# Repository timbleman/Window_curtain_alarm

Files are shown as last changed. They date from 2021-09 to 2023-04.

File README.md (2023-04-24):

# Window curtain alarm

## Basics
This project aims at creating an alarm that opens and closes a window curtain at certain times each weekday. The system is connected to the local network and is configured using socket communication. The alarm operates independently, it does not require a hub or external control, wake and sleep times can be set for each weekday. An internet connection is required.
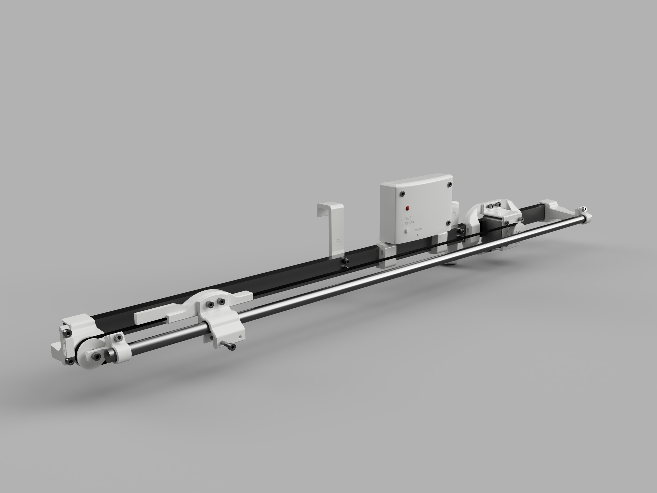
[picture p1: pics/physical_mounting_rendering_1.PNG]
Rendering of the physical hardware Hardware rendering.

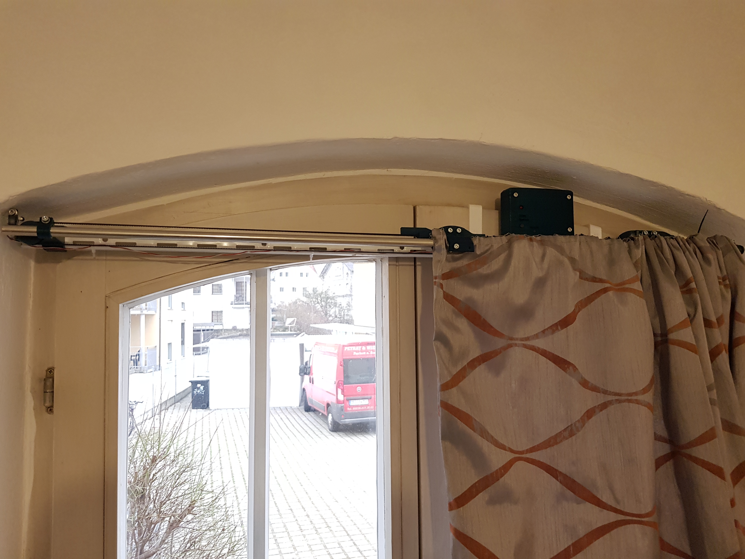
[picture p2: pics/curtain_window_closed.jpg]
Installed hardware. Window can still be opened.


## Changelog
* V1.2: Added OTA updating, WiFi connection using WPS and Serial, refactorings, a BOM and some UML diagrams.
* V1.1: Added a locally accessible, basic webpage. Improved 3D files slightly. Minor bug fixes.
* V1.0: Initial release. Controls using a hardware button and a TCP socket.

## Features
### Implemented features
* Automatically keeping track of time
* One wake and sleep time for each weekday
* Belt-driven opening and closing of curtains
* WiFi configuration using WPS, Serial interface or source code
* Socket-based user communication
* Local webpage for communication
* Over the air updating
* Button for snoozing one day and manually opening and closing the curtain
* PCB design
* STL files for assembling the project
### Possible future work
* Multiple wake and sleep times for each weekday
* Different endstop locations
* Using more advanced features of the TMC2209 stepper driver (e.g.: sensorless homing)
* Sync multiple curtains 
### Intentional limitations
* Only accessible in the local network
* No secure communication

## Usage
### Setup
Install the system according to the readme in /3D_objects/. In this directory there is also a bill of materials. You can adjust the SSID and password in the code. Compile and upload or just upload the binary.
Connect a 5V 2A power supply. If you have not provided your SSID in the code, you have two options: Firstly, you connect a Serial terminal with 9600 baud rate and enter your data. Secondly, you can use WPS if your router supports it. Press the WPS button of your router, then the button of the window_curtain_alarm, wait approximately 30 seconds and then restart the ESP.  
Assign a static IP using your router. You will need this IP to connect to the system. The IP is also printed using VCP at power-up.
### Basic controls using TCP sockets
This alarm can be configured using the telnet protocol. Connect using the IP and port 23 with a client of your choice.
Sending "help" gets a list of example commands.  
Upon powering up, the curtain position has to be calibrated. Open the curtain to the desired position by hand and 
send "calibrate". Make sure the motor moves in the right direction and hits the endstop. 
Now everything should be ready to go. Use "set_wake" and "set_sleep" to set the alarm. Check if the times have been correctly 
set using "waketimes" and "sleeptimes". Check if the right timezone is selected using "curtime".
You can manually move the curtain using "open", "close" or "curtainxor".  

<p float="left">
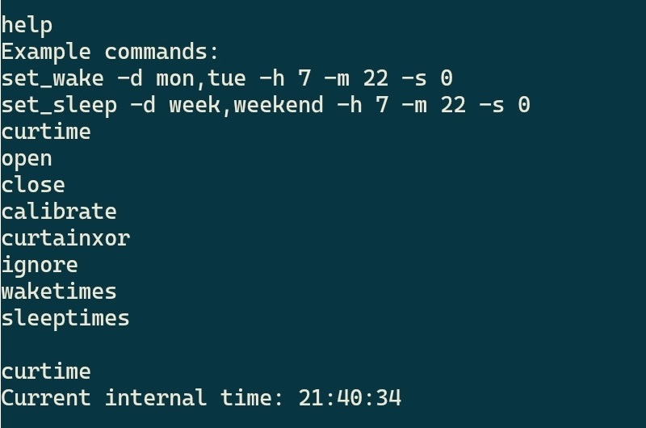
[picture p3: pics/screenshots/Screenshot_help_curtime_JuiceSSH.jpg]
  
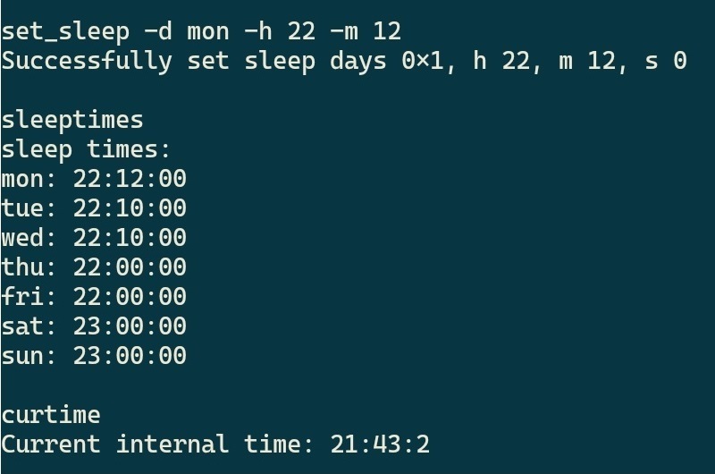
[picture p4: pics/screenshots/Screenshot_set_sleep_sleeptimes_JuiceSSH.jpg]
   
</p>

### Controls using the webpage
With version 1.1, a crude webpage is now available. Please don't judge the interface too harshly. :)  
The webpage is hosted locally and has the same functionality, as the command line style TCP interface. 
D-pad-like buttons allow you to move the curtain, ignore the next wake or calibrate.
Below, the current wake or sleep times are shown and can be changed.
The webpage should work on desktop and mobile. Some of the code has been taken from this [great post](https://gist.github.com/bbx10/667e3d4f5f2c0831d00b).  
You can update code when visiting IP:8000/update!
<p float="left">
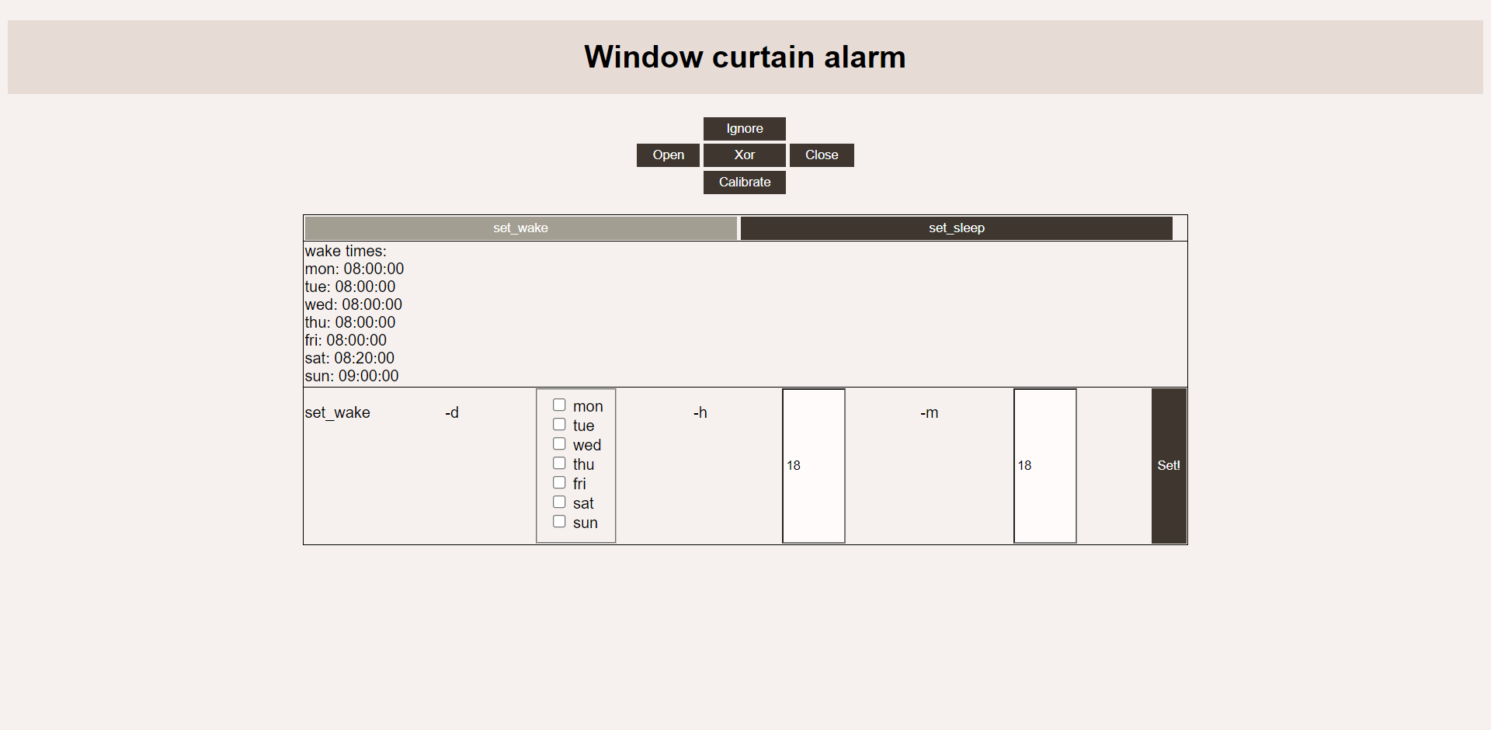
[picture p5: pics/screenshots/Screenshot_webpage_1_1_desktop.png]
  
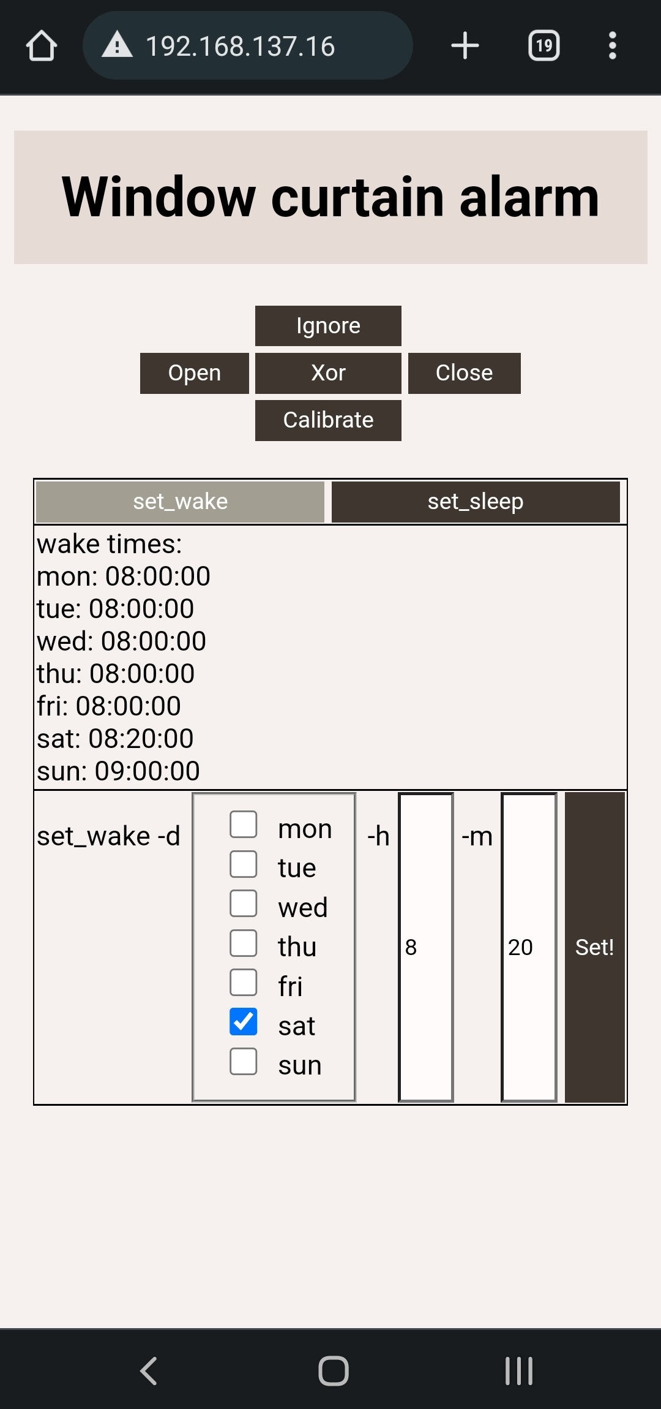
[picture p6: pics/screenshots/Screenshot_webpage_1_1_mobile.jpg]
   
</p>

### Controls using only the hardware
You can XOR the curtainstate by short pressing the hardware button, long pressing ignores the next wake.
An LED indicates if a short or a long press has been detected.

## Project structure
Here are some directories that may contain interesting files:
* /3D_objects/: 3D-printable objects and installation instructions.
* /course_python_draft/: This quick python prototype aims at visualizing the core concepts and ideas of the project. Untested.
* /curtain_wiring/: A KiCad project for the wiring diagram and PCB design.
* /esp8266_code/actual_project/: The unit tested proof of concept code ported to ESP8266.
* /esp8266_code/test_stuff/: Some quick projects testing basic functionality using the ESP8266.
  * /esp8266_code/test_stuff/socket_test/: TCP socket server test project for the ESP8266.
  * /esp8266_code/test_stuff/motor_test/: Homing and moving using the TMC2209 driver.
* /proof_of_concept/: Unit tested project implementing generic components. This project does not strictly target embedded hardware for ease of building and debugging.
* /pics/: Some pictures, diagrams and renderings.

## Implementation
### Hardware
Opening and closing the curtain is done using a belt driven by a stepper motor. A NEMA17 stepper in combination with a TMC2209 driver is currently used. The target platform is the ESP8266. This microcontroller has been chosen instead of a Raspberry PI due to its lower cost and power consumption. 
### Mounting
The hardware, including especially the motor, belt, and endstop, will be mounted using 3D printed objects. Currently, the project is not intended as a 'one design fits all' solution, but will need to be adapted to the used curtain and window.
### Programming language and environment
Due to its dominance in embedded systems and easier debugging, C, instead of C++, is used for most of the more generic project components. These components include user input parsing, keeping track of time, and controlling the IO.
As Arduino and most of its libraries are based on C++, the main function and socket server use this more high-level approach. The PlatformIO IDE and toolchain is used for the ESP8266 code. The unit tested proof of concept has been developed using CodeLite.  

The following class diagram should give an overview of the projects components.  As C, the language most used in this project is not class-oriented, I deviated slightly from the UML standard. Instead of modeling classes, I model files, structs, and enums. Enums are often used by multiple files, this is not modeled to increase readability.
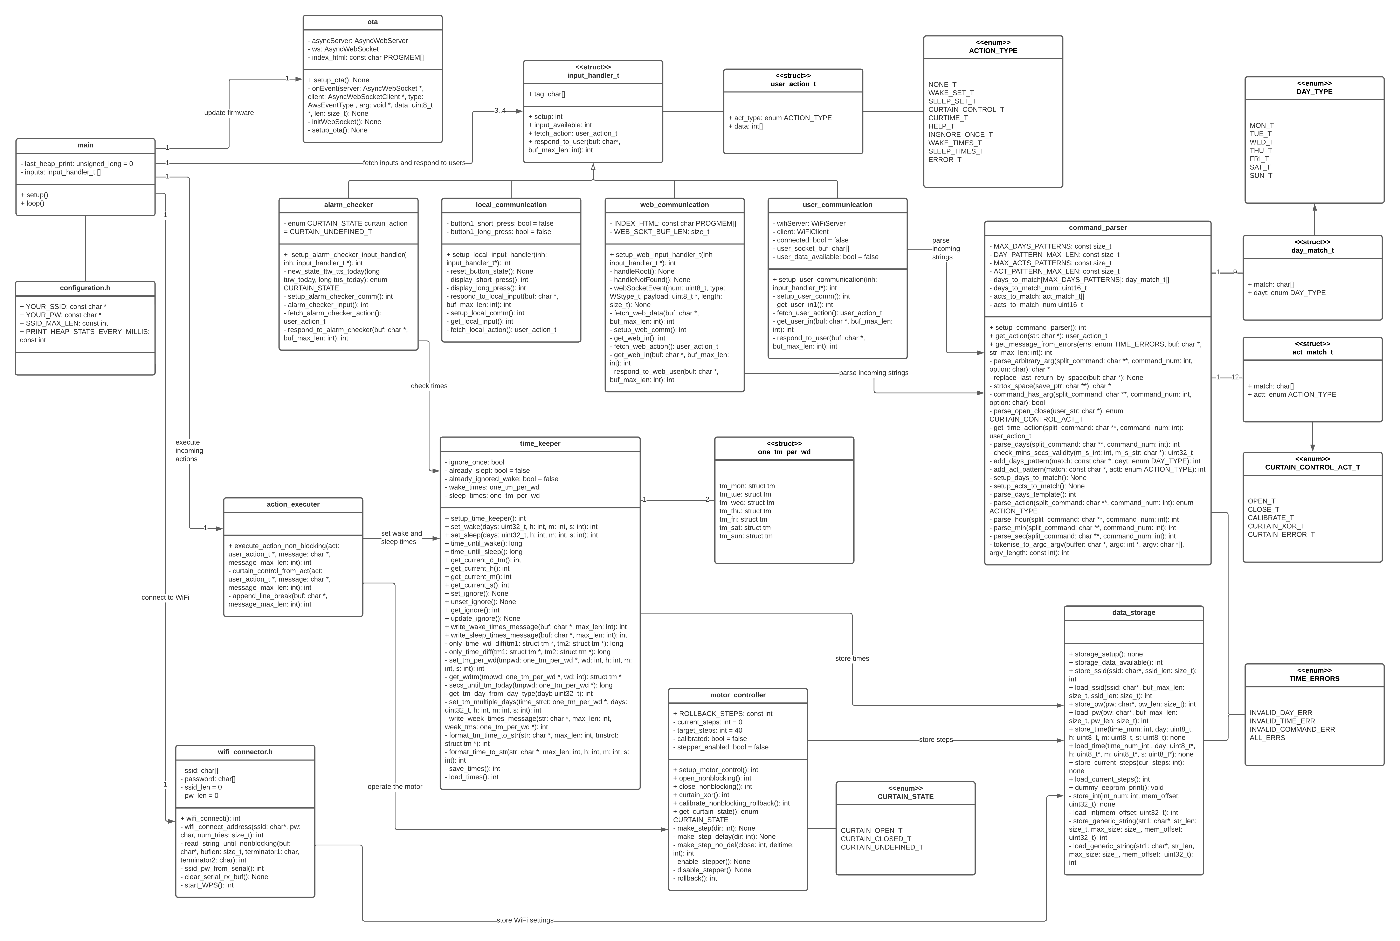
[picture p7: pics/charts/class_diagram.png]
A class diagram.

### Testing
The uCunit framework has been used for unit testing portable code components. The framework is basic but very portable and requires only a few header files.

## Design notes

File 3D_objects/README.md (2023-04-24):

# 3D objects and mounting

This subfolder stores 3D objects used to mount and build the curtain closer alarm.
The objects have been designed using Fusion360 and saved as STLs. Step files are also included.

## Project structure
These directories contain the 3D models:
* /electronics_mount/: Mounts for the board and the motor. Also includes the pulley and belt components.
* /motor_and_belt/: Components to install the Nema 17 and gt2 belt.
* /mount_curved_window/: Mounting brackets for a curved window. Will need to be adapted to your setup.
* /mount_rail/: Basic mounts for the rail. Includes end stop mount.

## Installation
### Needed components
You will need metric m4 screws of the following lengths: 10mm, 16mm, and 30mm. M3x6mm screws are also needed. You will also need square m4 nuts with dimensions of 7x7x2mm. The curtain rail has a diameter of 12mm. The flat u-shaped rail to mount all the components can be found in most German hardware stores. A 6mm wide gt2 belt and 684zz bearings are needed to move the curtain. Please look up the required electronic components in the wiring diagram. Have a look at the bill of meterials below, to find needed components.  

#### BOM
| Part name | Quantity | Price [€] |
|---|---|---|
| **Electronics** | | |
| ESP8266 NodeMCU ESP-12F | 1 | 5 |
| NEMA17 (max depth 34mm) | 1 | 7 |
| TMC2209 V2 | 1 | 3 |
| Board | 1 | 2 |
| R 100 Ohm | 1 | 0.01 |
| R 1 kOhm | 3 | 0.01 |
| R 10 kOhm | 2 | 0.01 |
| C 100 uF | 1 | 0.01 |
| C 220 uF | 1 | 0.01 |
| C 100 nF | 2 | 0.01 |
| LED 5mm | 1 | 0.01 |
| Button 12x12 | 1 | 0.01 |
| Pin headers m/f | Several  | 0.2 |
| Micro USB Cable | 1 | 5 |
| USB wall plug | 1 | 5 |
| **3D Printing** | | |
| Filament (PLA/PETG) | 200g | 4 |
| **Screws** | | |
| M3x6 | 4 | 0.1 |
| M4x4 grub screw | 1 | 0.1 |
| M4x10 | 22 | 0.3 |
| M4x16 | 4 | 0.1 |
| M4x30 | 3 | 0.1 |
| M4 7x7x2 square nuts | 29 | 0.2 |
| M4 washers | 25 | 0.2 |
| **Mounting** | | |
| GT2 belt 6mm | 3m | 3 |
| 684zz bearings | 2 | 2 |
| Curtain rod 12mm | 1.5m | 5 |
| Rail 10001 | 1.5m | 6 |
| **Total** | | ~50€ |

### Printing
As many of the components are under constant (but not very big) load, I would go with PETG instead of PLA, due to possible creep. The optimal print orientation should be obvious for most parts. Supports should only be needed for the belt connector. An end cap can be printed using TPU to prevent the metal curtain rail from directly hitting the wall. The beam holders require the m4 nuts to be inserted while printing. Remember to add pauses in the slicer! About 200g of Filament are needed.

### Installing everything
Cut the rails to the appropriate length and mount printed components using the m4 screws and nuts. Insert the curtain.
Mount the motor, the pulley, the roller with inserted bearings, and the gt2 belt. Tighten the belt either using the belt connector or the sliding motor mount. Solder components to the board. Install all electronic components. Mount the rail to your desired location and connect a micro USB cord to the NodeMCU.

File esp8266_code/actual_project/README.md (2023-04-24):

# Curtain closer alarm ESP8266 code
This directory contains the proof_of_concept curtain closer code adapted to the ESP8266, specifically the NodeMCU V3.

## Files of interest:
To get a quick overview, I will list which files do what. To keep it compact, only the headers are listed:
* /src/hardware_specific_code/: Code specifically written for the ESP.
    * /src/hardware_specific_code/networking/:
        * /src/hardware_specific_code/web_server/: Local website, webserver and websocket for user communication. Needs arduinoWebSockets library. OTA updating code.
        * user_communication.h: Handles TCP socket setup and communication.
        * wifi_conector.h: onnect to WiFi using SSID stored in EEPROM, specified at compiletime, Serial or WPS. 
    * /src/hardware_specific_code/local_hardware/:
        * data_storage.h: Stores the configuration. Uses the EEPROM library.
        * local_communication.h: Local (hardware, button) input and display.
        * motor_controller.h: This file handles the calibration and operation of the motor.
* /src/portable_code/: Portable, unit tested code.
    * action_executer.h: Executes an action created by the command_parser.
    * alarm_checker.h: Checks whether the curtain should be opened or closed now. Has to be called in a loop. 
    * command_parser.h: Here user input strings are parsed into an action type.
    * time_keeper.h: Saves wake and sleep times for each weekday. Keeps track of time.
    * types_and_enums.h: Type and enum definitions that are shared between multiple components.
* /src/configuration.h: Configures project build and testsuite execution.
* /src/main.cpp: This is the main file running the main loop.

## Configuration
There are some configuration parameters.
SSID and your WIFI password can be set in *configuration.h*. You can also skip this step and directly throw the binary on the ESP and connect to WiFi via Serial or WPS. Look at the main README.md for further instructions.  
The UTC time offset will need to be set in main.c using the `setenv()` function.  
The speed of the stepper motor can be adjusted in motor_controller.c using `FAST_STEP_TIME` and `SLOW_STEP_TIME`.  
Most prints can be disabled using define statements.

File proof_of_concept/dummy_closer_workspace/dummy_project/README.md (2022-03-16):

# Window curtain alarm proof of concept

## Intro
This project serves as a quick prototype for a window curtain alarm.
Basic functions are implemented and tested without the actual hardware:
Parsing strings, setting, and keeping track of time will be fully implemented.
New code should be tested at first in this project before being ported to a MCU.
The motor control and socket interaction will only be implemented as a dummy, as these are highly platform-dependent.
Extensive unit testing using the uCUnit framework should reduce the amount of debugging on the embedded platform.

## Files and contents
This section quickly discusses the files and their contents.
For simplicity reasons, only the h-file is described, not the implementation.
* action_executer.h: Executes an action created by the command_parser.
* alarm_checker.h: Checks whether the curtain should be opened or closed now. Has to be called in a loop. 
* command_parser.h: Here user input strings are parsed into an action type.
* configuration.h: Configures project build and test suite execution.
* data_storage.h: A dummy file to test storing data. Resembles the EEPROM library. 
* main.c: This is the main file running the main loop.
* motor_controller.h: This file handles the calibration and operation of the motor.
* System.c: This file is for the uCUnit framework. The print function has to be changed when porting. 
* Testsuite.h: The actual test cases run by the uCUnit framework. 
* time_keeper.h: Saves wake and sleep times for each weekday. Keeps track of time.
* types_and_enums: Type and enum definitions that are shared between multiple components.
* uCUnit-v1.0.h: A lightweight unit testing framework.

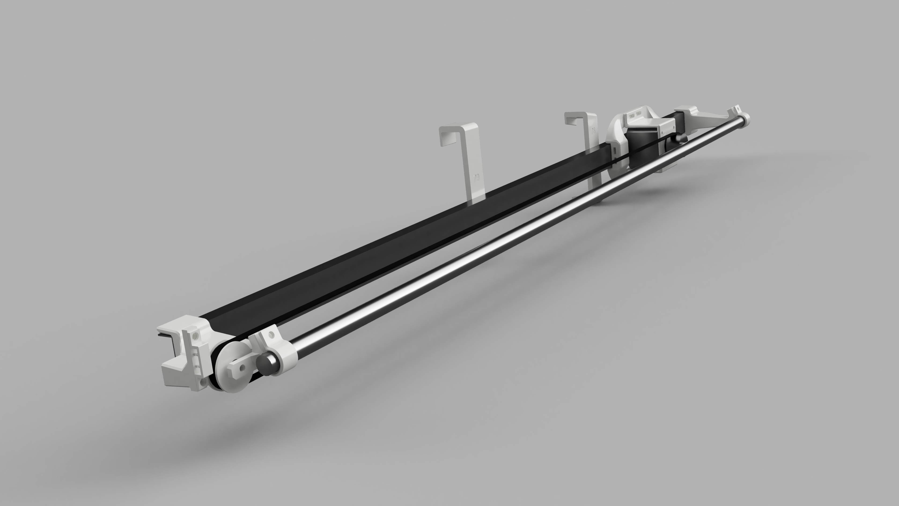
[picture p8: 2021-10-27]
pics/physical_mounting_rendering.PNG

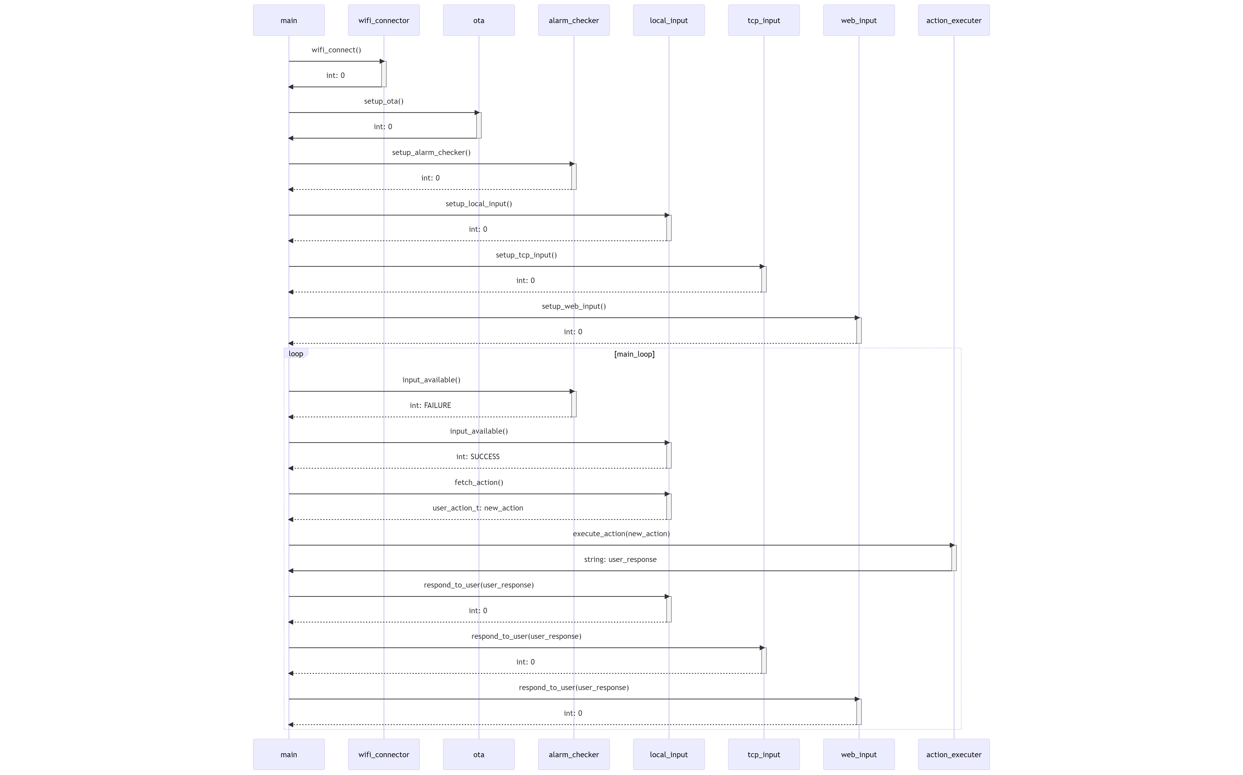
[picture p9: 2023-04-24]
pics/charts/main_flow_chart.png

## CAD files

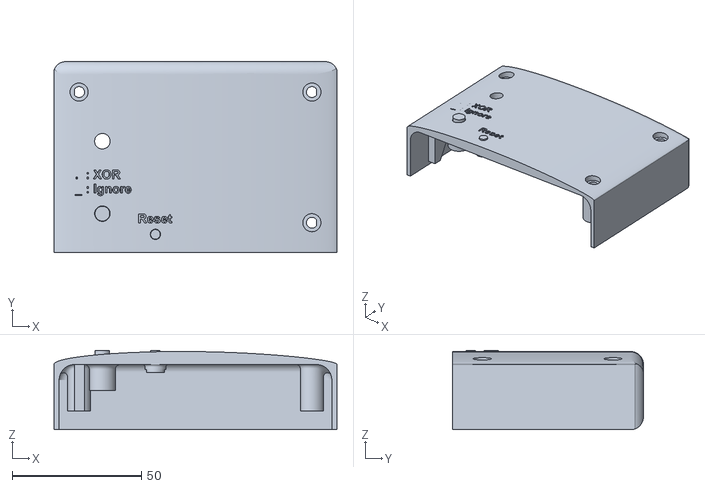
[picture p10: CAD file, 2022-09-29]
3D_objects/electronics_mount/pcb_cover_v1_1.stl
109.4 x 73.8 x 30.7

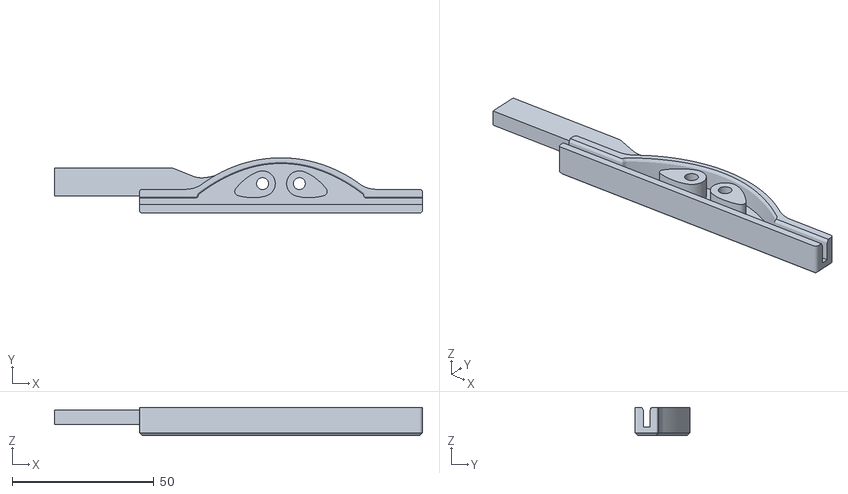
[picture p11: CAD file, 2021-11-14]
3D_objects/motor_and_belt/belt_connector_v1.stl
130.0 x 19.5 x 10.00

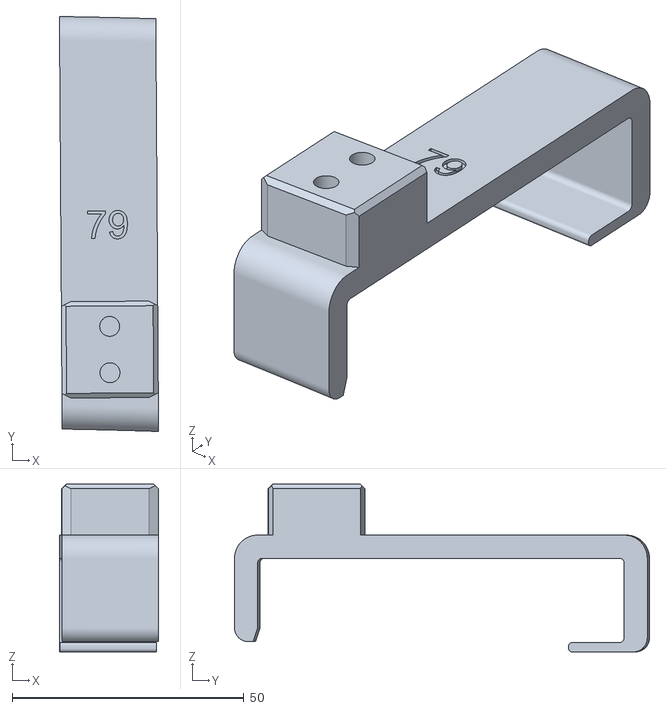
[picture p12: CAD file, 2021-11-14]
3D_objects/mount_curved_window/leftmost_holder_78_v1.stl
21.4 x 89.5 x 36.2

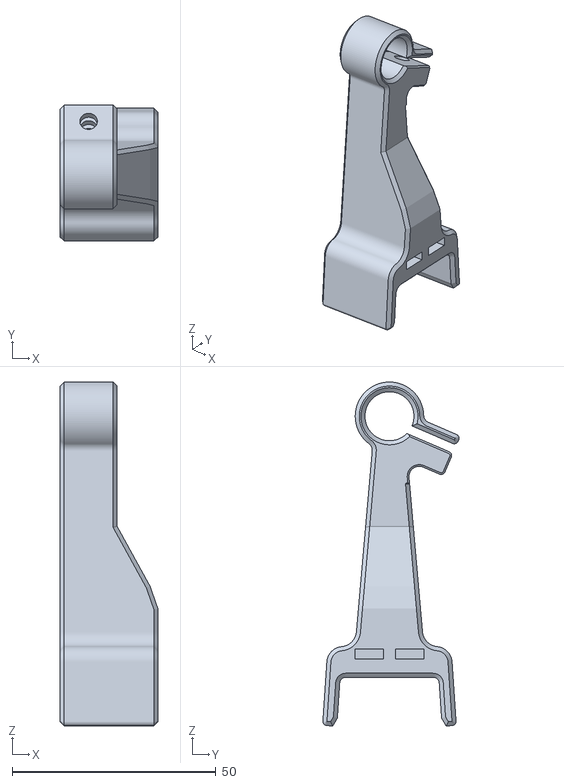
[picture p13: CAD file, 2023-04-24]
3D_objects/mount_rail/beam_holder_r_longer_v1_2.stl
24.0 x 33.4 x 84.3

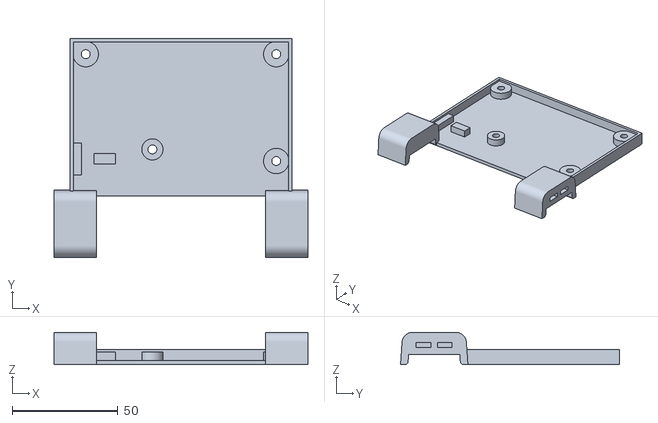
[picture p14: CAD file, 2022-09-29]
3D_objects/electronics_mount/pcb_holder_v1_1.stl
120.0 x 103.5 x 15.3

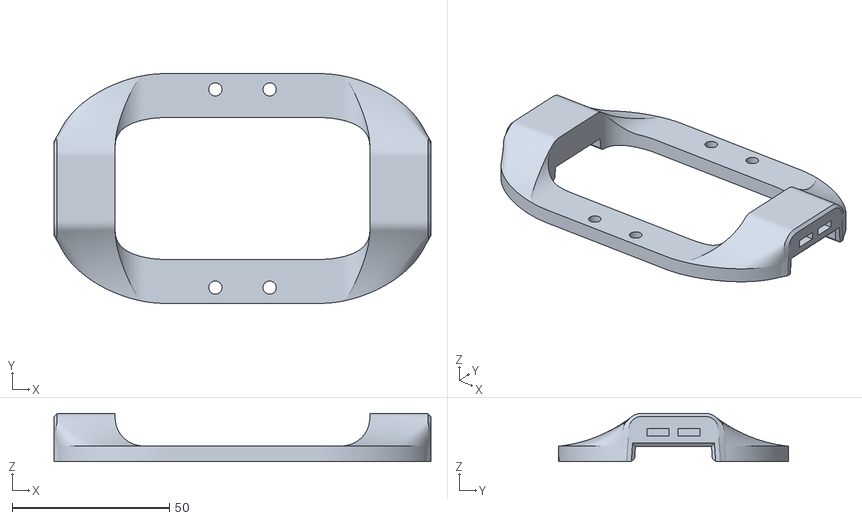
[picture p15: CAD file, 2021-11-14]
3D_objects/motor_and_belt/motor_holder_curved_v1.stl
120.0 x 73.1 x 15.3

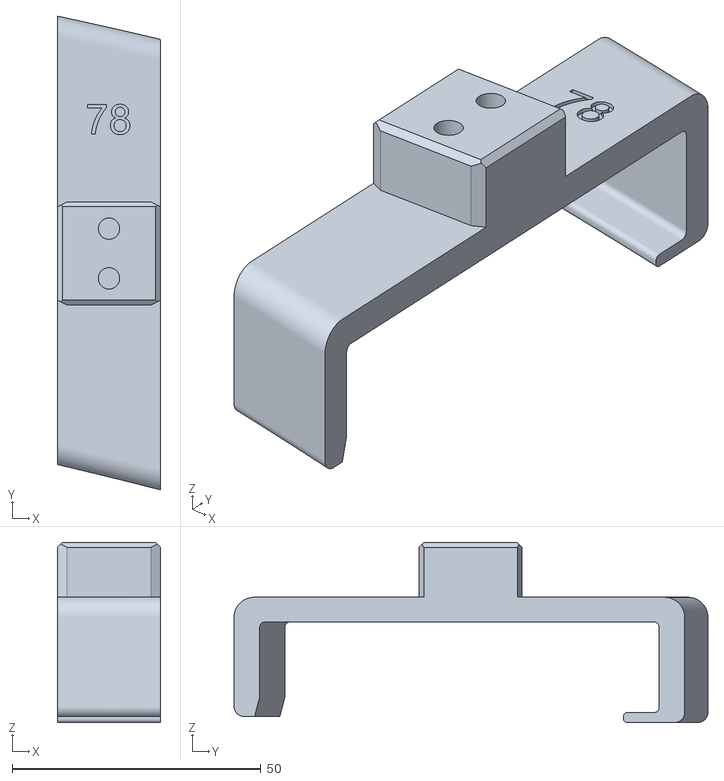
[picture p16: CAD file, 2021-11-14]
3D_objects/mount_curved_window/right_holder_78_v1.stl
20.8 x 95.3 x 36.2

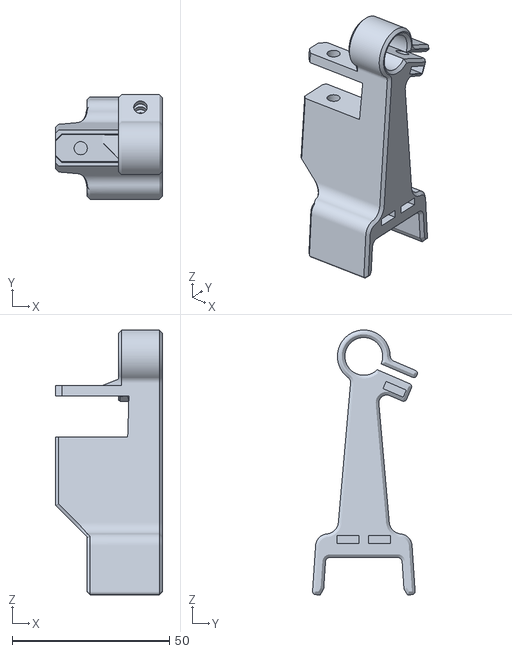
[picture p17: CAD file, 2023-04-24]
3D_objects/mount_rail/beam_holder_l_longer_v1_2.stl
34.0 x 33.4 x 84.3

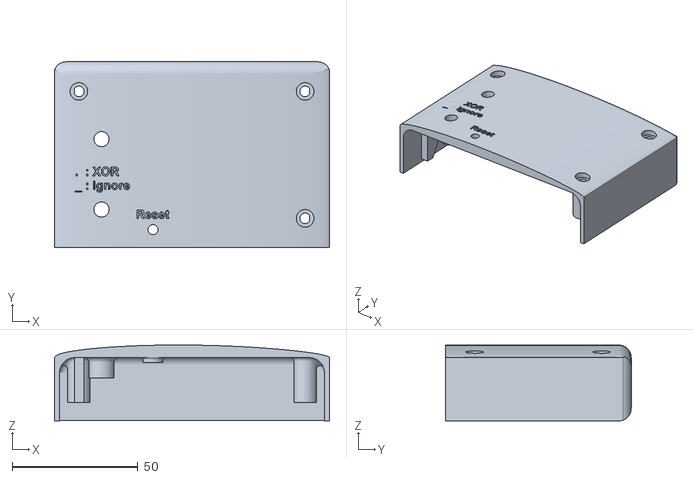
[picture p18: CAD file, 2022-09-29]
3D_objects/electronics_mount/pcb_cover_rounded_v1_1.stl
109.4 x 73.8 x 30.2

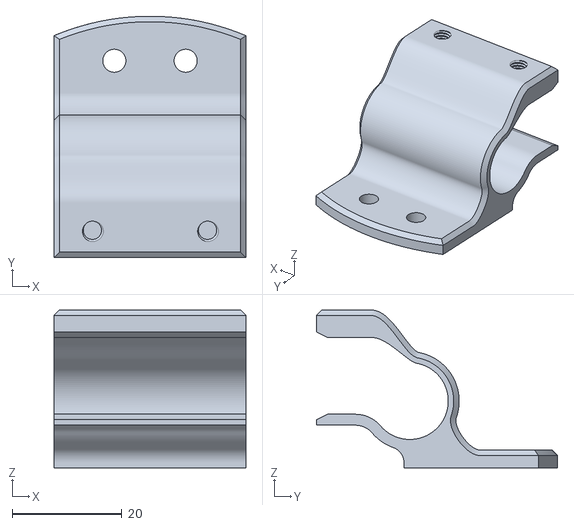
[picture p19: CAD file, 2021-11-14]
3D_objects/motor_and_belt/curtain_connector_v1.stl
35.0 x 44.0 x 28.8

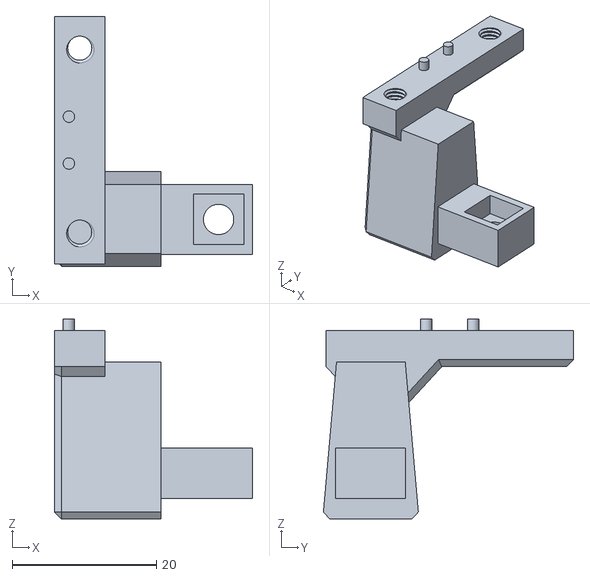
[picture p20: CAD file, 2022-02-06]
3D_objects/mount_rail/micro_switch_holder_v1.stl
27.5 x 34.7 x 27.7

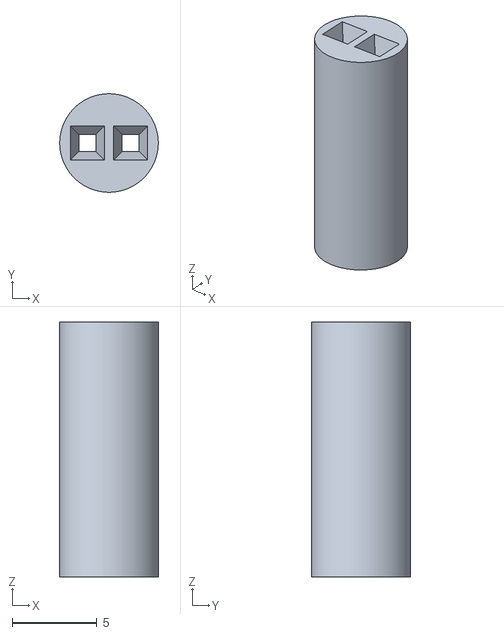
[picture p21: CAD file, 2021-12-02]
3D_objects/electronics_mount/5mm_led_standoff_v1.stl
5.80 x 5.80 x 15.0

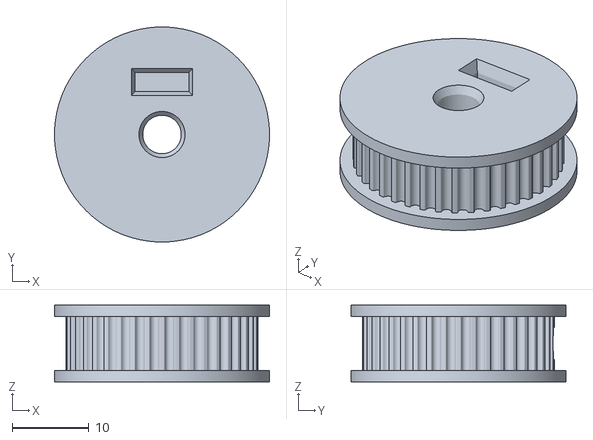
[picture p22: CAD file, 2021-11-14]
3D_objects/motor_and_belt/gt2_pulley_v1.stl
28.0 x 28.0 x 10.0

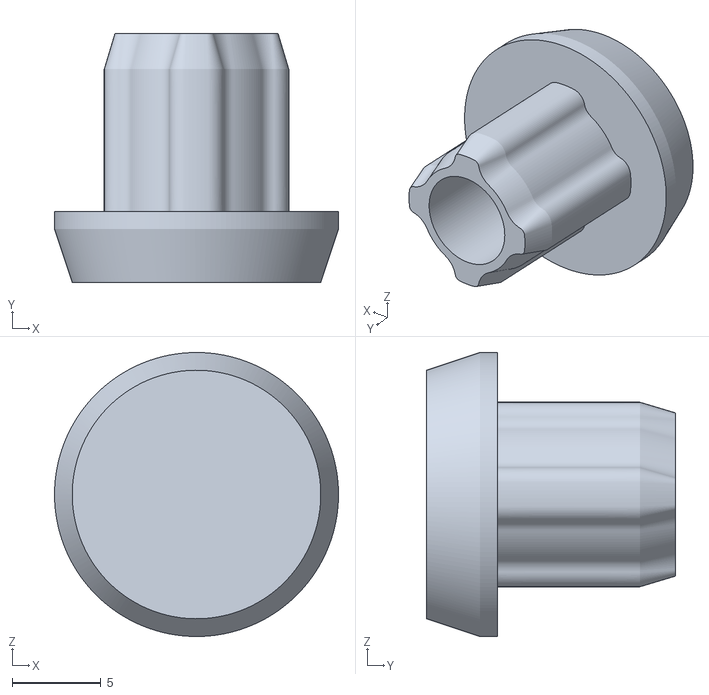
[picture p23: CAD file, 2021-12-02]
3D_objects/mount_rail/tail_tpu_damper_v1.stl
16.0 x 14.0 x 16.0

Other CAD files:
3D_objects/motor_and_belt/nema_holder_v1.stl
3D_objects/mount_rail/micro_switch_cover_v1.stl
3D_objects/electronics_mount/reset_button_v1.stl
3D_objects/motor_and_belt/roller_inner_spacer_v1.stl
3D_objects/electronics_mount/pcb_holder_v1.stl
3D_objects/electronics_mount/user_button_v1.stl
3D_objects/motor_and_belt/belt_connector_lid_v1.stl
3D_objects/motor_and_belt/custom_roller_v1.stl
3D_objects/motor_and_belt/roller_spacer_v1.stl

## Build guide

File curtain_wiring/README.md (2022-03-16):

# Wiring
This directory contains a wiring diagram and a PCB design. Created using KiCad.

## Wiring
This wiring diagram is also present as a PDF. Please refer to the document for needed components. 
Low noise power supplies are expected, if the input voltage is noisy you may need to add some components.

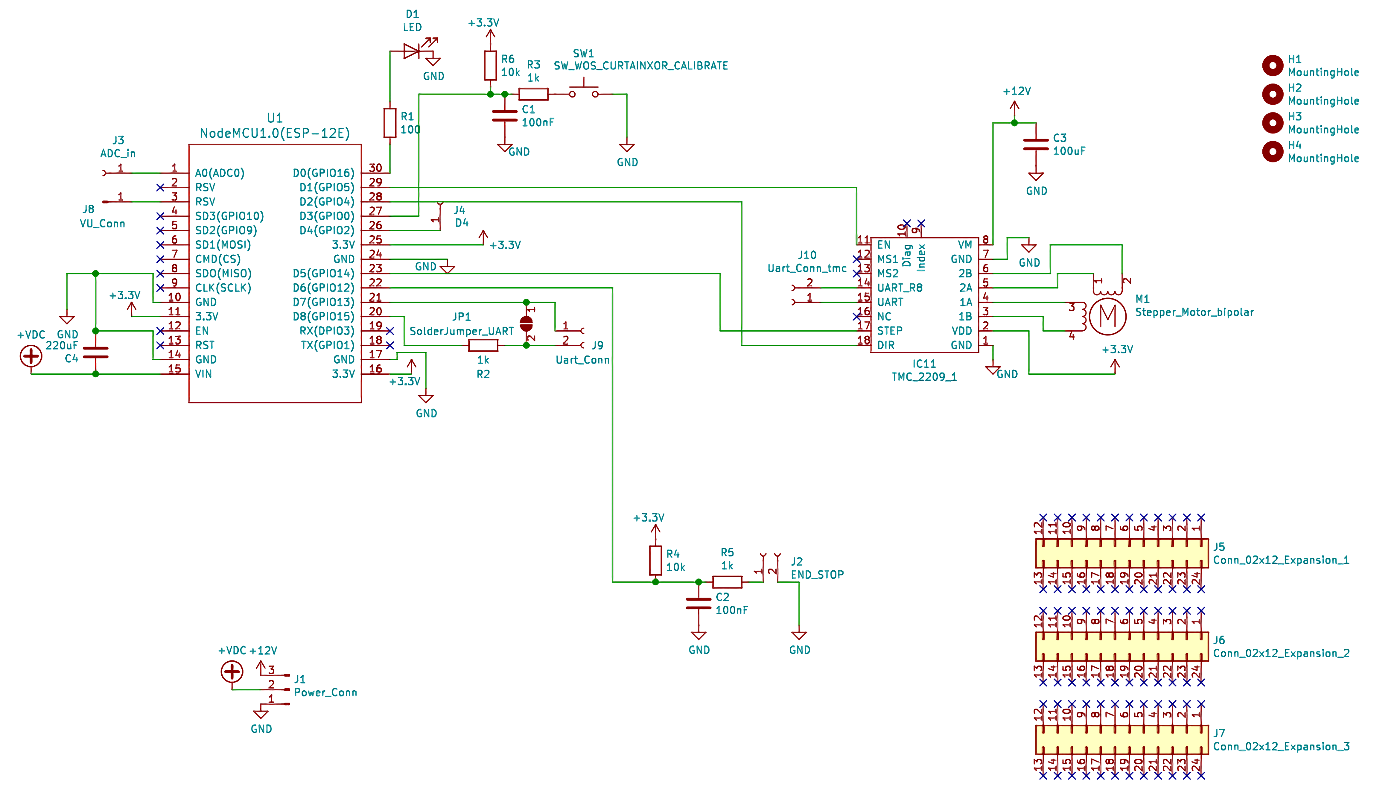
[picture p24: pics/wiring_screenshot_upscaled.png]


## PCB
This is the board designed for the curtain alarm. 
The board has a status LED and a button for user input. 
To fit inside the 3D printed housing, the ESP8266 (NodeMCU 12E) and TMC2209 should be socketed. The LED standoff needs to be installed.  
The stepper driver and ESP can use separate power supplies. This is recommended to avoid noise. 
Theoretically, you could power both the ESP and motor using the micro USB port and connecting the ESPs VU to the TMCs VM.
If you detect power-related problems (like crashing when the motor starts turning), you could add some additional filtering. 
There is some additional space to include some components like a low pass filter.   
While the code does not yet utilize the TMCs UART functionality, the board is ready for it. Depending on the desired mode of communication, J9, J10, or JP1 need to be connected. 
R2 may need to be added.

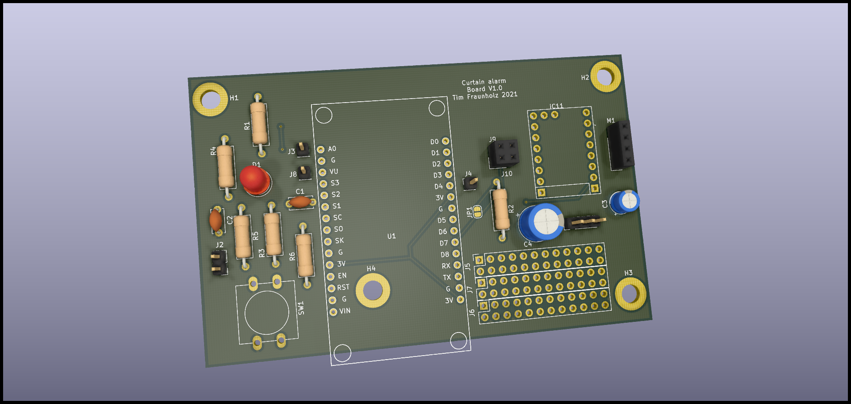
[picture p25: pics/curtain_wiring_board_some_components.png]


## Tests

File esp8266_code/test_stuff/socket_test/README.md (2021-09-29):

# Socket test

This project tests basic user interaction as a socket server.
The arduino platform is used on the ESP8266 MCU.

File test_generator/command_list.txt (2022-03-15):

Paste these lines into a telnet client of your choice
set_wake -d week,sat,sun -h 12 -m 1 
set_sleep -d week,sat,sun -h 12 -m 2 
set_wake -d week,sat,sun -h 12 -m 3 
set_sleep -d week,sat,sun -h 12 -m 4 
set_wake -d week,sat,sun -h 12 -m 5 
set_sleep -d week,sat,sun -h 12 -m 6 
set_wake -d week,sat,sun -h 12 -m 7 
set_sleep -d week,sat,sun -h 12 -m 8 
set_wake -d week,sat,sun -h 12 -m 9 
set_sleep -d week,sat,sun -h 12 -m 10

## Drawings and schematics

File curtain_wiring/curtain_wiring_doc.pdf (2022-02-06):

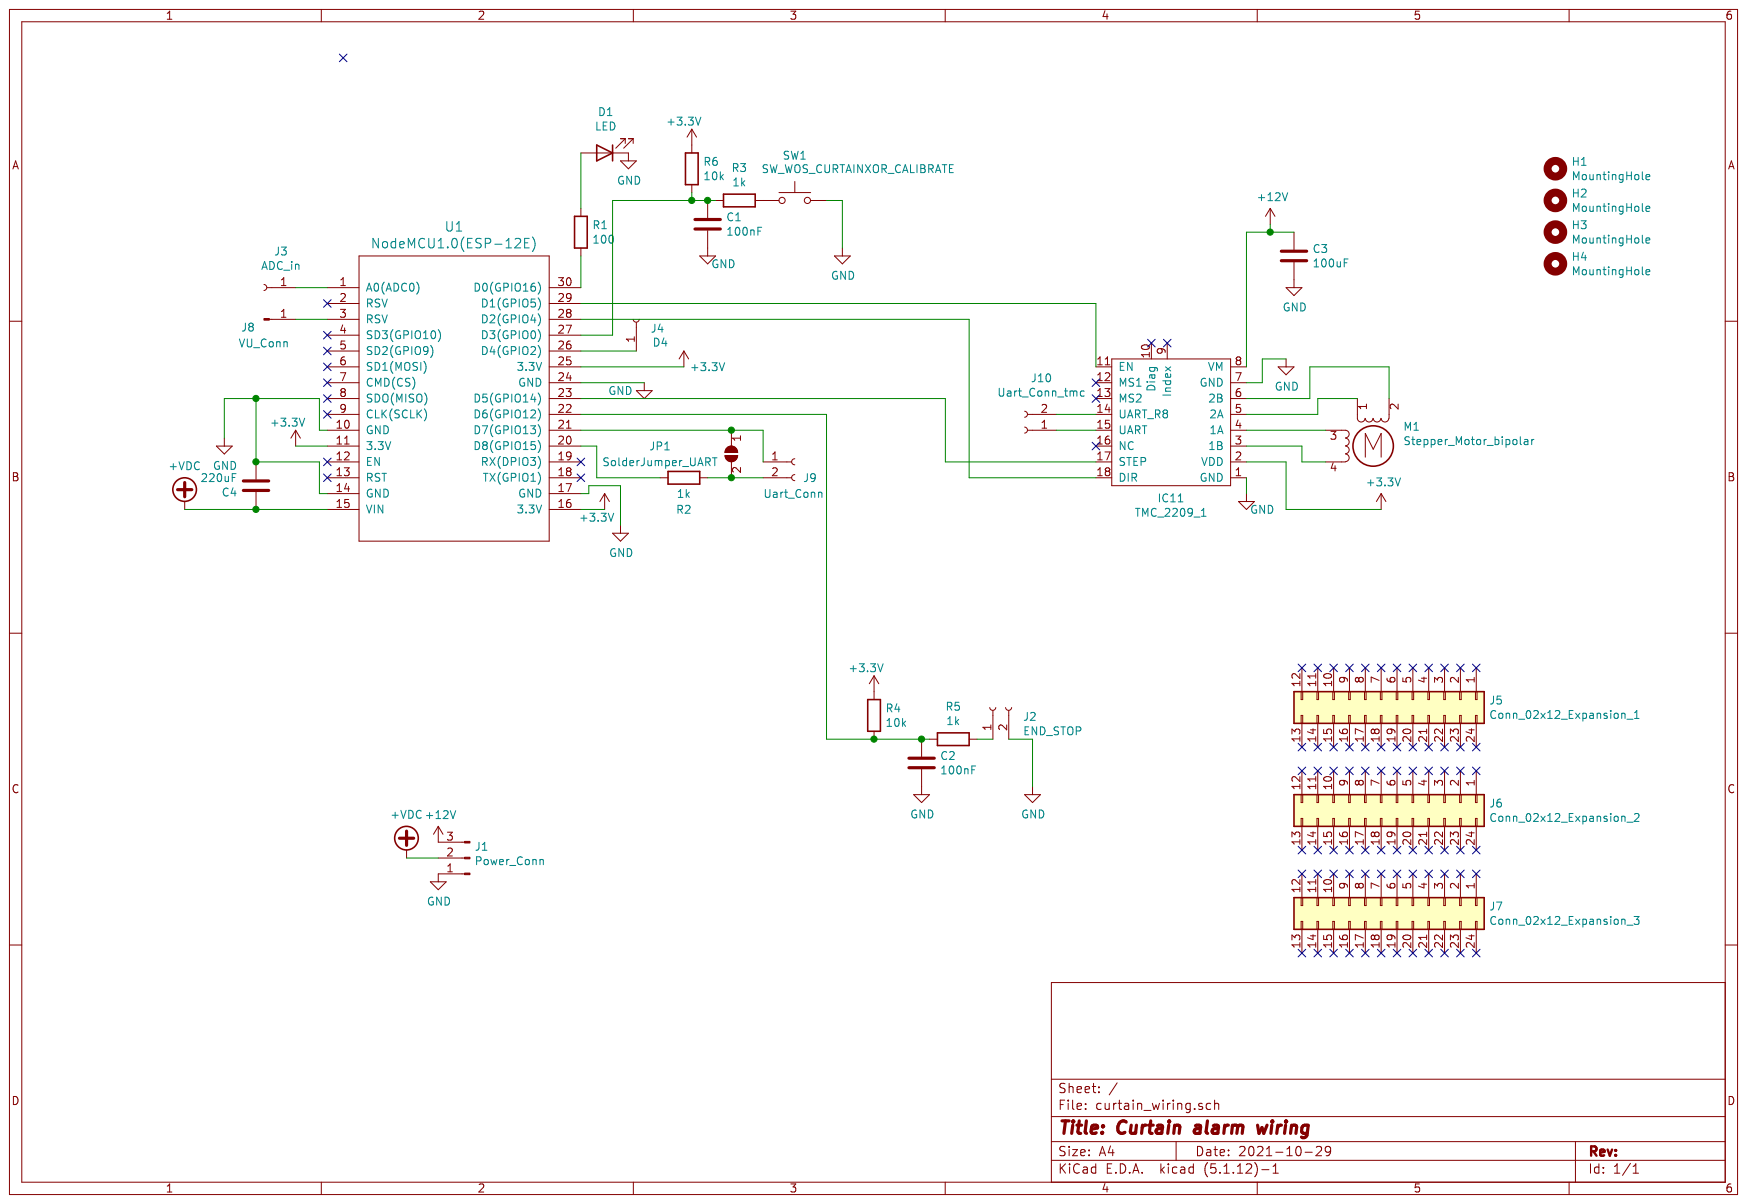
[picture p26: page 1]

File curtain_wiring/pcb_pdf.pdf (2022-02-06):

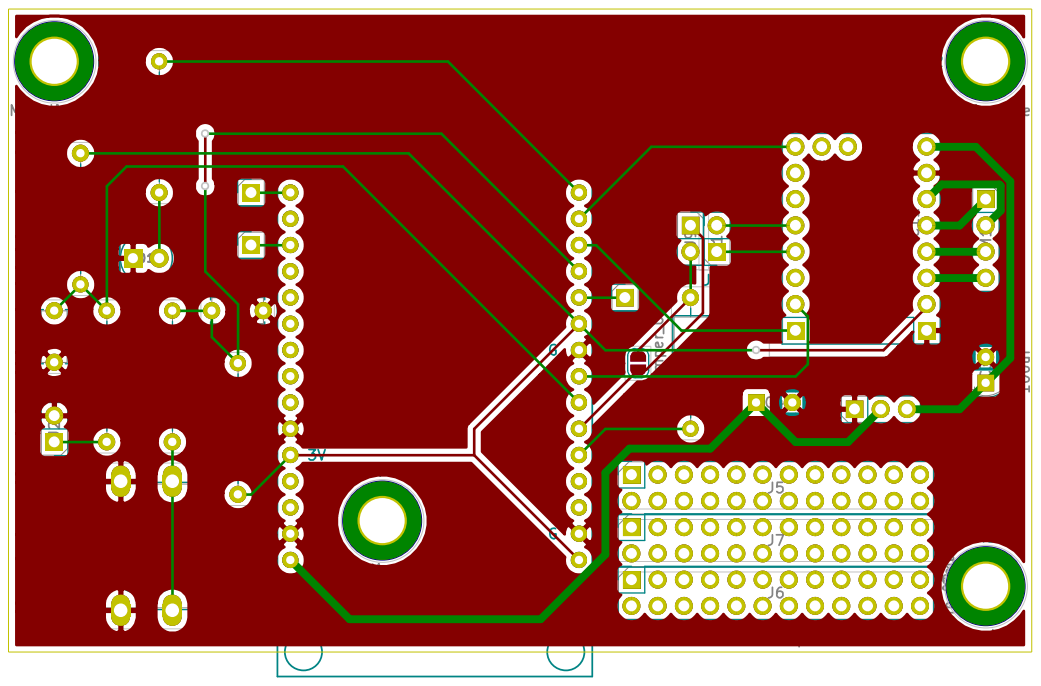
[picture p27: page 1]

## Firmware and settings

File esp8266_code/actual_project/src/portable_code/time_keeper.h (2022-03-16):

/*
 * The time keeper keeps track of the current time and sleep and wake times.
 * To be able to achieve multiple sleep/wake times a day, a major refactoring
 * would be required.
 */

#ifndef _TIME_KEEPER_H_
#define _TIME_KEEPER_H_

#ifdef __cplusplus
extern "C" {
#endif

/********************************** Includes **********************************/
#include <stdint.h>
#include "configuration.h"

#ifdef TESTABLE_TK_CODE
#include <time.h>
#endif // TESTABLE_TK_CODE


/********************************* Constants *********************************/
#define DEFAULT_WEEKEND_WAKE 9
#define DEFAULT_WEEK_WAKE 8
#define DEFAULT_SLEEP 23


/***************************** Struct definitions *****************************/
#ifdef TESTABLE_TK_CODE
typedef struct {
    struct tm tm_mon;
    struct tm tm_tue;
    struct tm tm_wed;
    struct tm tm_thu;
    struct tm tm_fri;
    struct tm tm_sat;
    struct tm tm_sun;
} one_tm_per_wd;
#endif // TESTABLE_TK_CODE


/**************************** Variable definitions ****************************/
#ifdef TESTABLE_TK_CODE
one_tm_per_wd wake_times;
one_tm_per_wd sleep_times;
#endif // TESTABLE_TK_CODE


/**************************** Prototype functions ****************************/
/*
 * Default wake and sleep times are set for each weekday.
 * 
 * @return: 0 if successful.
 */
int setup_time_keeper();

/*
 * Set the time to wake up for multiple days.
 * Days are onehot encoded as in the DAY_TYPE defined in command_parser.
 * Unsets ignore of a single wake.
 * 
 * @param days: The weekdays to set.
 * @param h: The hour to open the curtain.
 * @param m: The minute to open the curtain.
 * @param s: The second to open the curtain.
 * @return: 0 if successful.
 */
int set_wake(uint32_t days, int h, int m, int s);

/*
 * Set the time to sleep for multiple days.
 * Days are onehot encoded as in the DAY_TYPE defined in command_parser.
 * Unsets ignore of a single wake.
 * 
 * @param days: The weekdays to set.
 * @param h: The hour to close the curtain.
 * @param m: The minute to close the curtain.
 * @param s: The second to close the curtain.
 * @return: 0 if successful.
 */
int set_sleep(uint32_t days, int h, int m, int s);

/*
 * The time difference from now until the wake time of the current weekday.
 * Positive if one_tm_per_wd entry is in the future, negative if in the past.
 * 
 * @return: Difference in seconds.
 */
long time_until_wake();

/*
 * The time difference from now until the sleep time of the current weekday.
 * Positive if one_tm_per_wd entry is in the future, negative if in the past.
 * 
 * @return: Difference in seconds.
 */
long time_until_sleep();

/*
 * To check the current system time.
 * Copy by value is performed, should not be called all the time.
 * 
 * @return: The current day in the C tm struct format.
 */
int get_current_d_tm();

/*
 * To check the current system time.
 * Copy by value is performed, should not be called all the time.
 * 
 * @return: The current hour.
 */
int get_current_h();

/*
 * To check the current system time.
 * Copy by value is performed, should not be called all the time.
 * 
 * @return: The current minute.
 */
int get_current_m();

/*
 * To check the current system time.
 * Copy by value is performed, should not be called all the time.
 * 
 * @return: The current second.
 */
int get_current_s();


/*
 * The time keeper is able to ignore the next wake.
 * Call this if the next wake should be ignored.
 * 
 * @return: None.
 */
void set_ignore();

/*
 * The time keeper is able to ignore the next wake.
 * Call this if the next wake should no longer be ignored.
 * 
 * @return: None.
 */
void unset_ignore();

/*
 * The time keeper is able to ignore the next wake.
 * Check if the next wake should be ignored.
 * 
 * @return: 1 if to be ignored, 0 if not.
 */
int get_ignore();

/*
 * The time keeper is able to ignore the next wake.
 * For the ignore to be correctly updated, this function nedds to be called 
 * repeatedly.
 * 
 * @return: None.
 */
void update_ignore();

/*
 * Get all the wake times in a user readable format.
 * 
 * @param buf: String buffer to write into.
 * @param max_len: The maximum length of the string.
 * @return: Success if 0.
 */
int write_wake_times_message(char *buf, int max_len);

/*
 * Get all the sleep times in a user readable format.
 * 
 * @param buf: String buffer to write into.
 * @param max_len: The maximum length of the string.
 * @return: Success if 0.
 */
int write_sleep_times_message(char *buf, int max_len);

#ifdef TESTABLE_TK_CODE
int format_time_to_str(char *str, int max_len, int h, int m, int s);
#endif // TESTABLE_TK_CODE

#ifdef __cplusplus
}
#endif

#endif // _TIME_KEEPER_H_

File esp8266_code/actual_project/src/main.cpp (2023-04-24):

/********************************** Includes **********************************/
#include <Arduino.h>
#include <stdint.h>
#include "ESP8266WiFi.h"
#include "configuration.h"
#include "hardware_specific_code/networking/web_server/ota/ota.h"
#include "hardware_specific_code/networking/user_communication.h"
#include "configuration.h"
#ifndef UNITTESTS_INSTEAD_OF_MAIN
#include "portable_code/action_executer.h"
#include "portable_code/alarm_checker.h"
#include "portable_code/command_parser.h"
#include "hardware_specific_code/local_hardware/data_storage.h"
#include "hardware_specific_code/local_hardware/local_communication.h"
#include "hardware_specific_code/networking/web_server/web_communication.h"
#include "hardware_specific_code/local_hardware/motor_controller.h"
#include "hardware_specific_code/networking/wifi_connector.h"
#include "portable_code/time_keeper.h"
#include "portable_code/types_and_enums.h"
#else
#include "Testsuite.h"
#endif // UNITTESTS_INSTEAD_OF_MAIN
#include "time.h" // setenv(), do not worry about IDE warning, compiles fine


/********************************** Defines **********************************/
#define RESPOND_BUF_SIZE 256
#ifndef ENABLE_LOCAL_WEB_SITE
#define NUM_INPUTS 3
#else
#define NUM_INPUTS 4
#endif // ENABLE_LOCAL_WEB_SITE


/********************************* Constants **********************************/
/***************************** Struct definitions *****************************/
/**************************** Prototype functions *****************************/
/**************************** Variable definitions ****************************/
#ifdef PRINT_HEAP_STATS_EVERY_MILLIS
unsigned long last_heap_print = 0;
#endif // PRINT_HEAP_STATS_EVERY_MILLIS

// Manage multiple inputs: input_handler_t 
input_handler_t inputs[NUM_INPUTS] = {0};


/**************************** Function definitions ****************************/
void setup() {
  Serial.begin(9600);
  delay(1000);

#ifndef UNITTESTS_INSTEAD_OF_MAIN
  storage_setup();

  setup_command_parser();

  setup_motor_control();

  /*
   * This allows the correct timeoffset to be used for localtime().
   * Do not worry about the IDE warning, the function is defined in a macro.
   */
  setenv("TZ", "CET-1CEST,M3.5.0,M10.5.0/3", 3);
 
  wifi_connect();

  setup_time_keeper();
  printf("cur time %i %i %i \n", get_current_h(), get_current_m(), get_current_s());

  // Setup input_handler_t
  setup_alarm_checker_input_handler(&inputs[0]);
  setup_user_input_handler_t(&inputs[1]);
  setup_local_input_handler_t(&inputs[2]);
#ifdef ENABLE_LOCAL_WEB_SITE
  setup_web_input_handler_t(&inputs[3]);

  setup_ota();
#endif // ENABLE_LOCAL_WEB_SITE
#endif // UNITTESTS_INSTEAD_OF_MAIN
}

void loop() {
#ifndef UNITTESTS_INSTEAD_OF_MAIN
  static char buf[RESPOND_BUF_SIZE] = {0};
  static bool busy = false;
  static user_action_t usr_act;

  // Check for new input if no action is currently executed.
  for (int i = 0; i < NUM_INPUTS; i++)
  {
    input_handler_t *current_input = &inputs[i];
    if (!busy)
    {
      if (current_input->input_available() == 0)
      {
        usr_act = current_input->fetch_action();
        busy = true;
      }
    }
  }
  
  // Execute an action and respond back to all users when done
  if (busy)
  {
    // Execute an action.
    busy = execute_action_non_blocking(&usr_act, buf, RESPOND_BUF_SIZE);
    if ((!busy) && (strlen(buf) > 0))
    {
      for (int i = 0; i < NUM_INPUTS; i++)
      {
        input_handler_t *current_input = &inputs[i];
        current_input->respond_to_user(buf, strlen(buf));
      }
      memset(buf, 0, RESPOND_BUF_SIZE);
    }
  }

#ifdef PRINT_HEAP_STATS_EVERY_MILLIS
  /* 
   * There seem to be no memory leaks. 
   * I will, however, still leave this code as it does not hurt to check.
   */
  if (millis() - last_heap_print > PRINT_HEAP_STATS_EVERY_MILLIS)
  {
    printf("Free heap: %u, heap fragmentation: %u\n\r", ESP.getFreeHeap(),
            ESP.getHeapFragmentation());
    last_heap_print = millis();
  }
#endif // PRINT_HEAP_STATS_EVERY_MILLIS
#endif // UNITTESTS_INSTEAD_OF_MAIN
}

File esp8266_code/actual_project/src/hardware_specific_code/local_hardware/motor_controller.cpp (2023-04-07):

/********************************** Includes **********************************/
#include <Arduino.h>
#include "motor_controller.h"
#include "data_storage.h"
#include "../../configuration.h"


/********************************* Constants **********************************/
#define STEPPER_ENABLE_PIN D1
#define STEPPER_DIR_PIN D2
#define PERFORM_STEP_PIN D5
#define END_STOP_PIN D6

// Time in ms between steps. Controls the motor speed.
// TODO In mm/s
#define FAST_STEP_TIME 400
#define SLOW_STEP_TIME 800


/***************************** Struct definitions *****************************/
/**************************** Prototype functions *****************************/
void make_step(int dir);
void make_step_delay(int dir);
int make_step_no_del(int close, int deltime);
void enable_stepper();
void disable_stepper();
int rollback();


/**************************** Variable definitions ****************************/
#ifndef TESTABLE_MOTOR_CODE
int current_steps = 0;
int target_steps = 40;
#endif // TESTABLE_MOTOR_CODE
bool calibrated = false;
bool stepper_enabled = false;


/**************************** Function definitions ****************************/
/*
 * Notes concerning the ESP8266:
 * ESP8266 console used UART0 by default (RX and TX pins).
 * Other UARTs: RXD2 (D7, GPIO16), TXD2 (D8, GPIO17), RXD1 (SD1, SD_DATA_1), 
 * TXD1 (D4, GPIO2)
 * 
 * Pins that are most likely not relevant for the project:
 * D1 GPIO5 (SCL), D2 GPIO4 (SDA), D5 GPIO14 (SCLK), D6 GPIO12 (MISO)
 */

/*
 * Notes concerning the TMC2209:
 * Passive breakmode can be enabled using UART.
 * Default current is about 0.5A. This is enough at 5v for curtain operation.
 */

/*
 * Sets up variables of this file. Configures inputs and outputs.
 * 
 * @return: 0 if successful.
 */
int setup_motor_control()
{
    // Setup pins
    pinMode(STEPPER_ENABLE_PIN, OUTPUT);
    pinMode(STEPPER_DIR_PIN, OUTPUT);
    pinMode(PERFORM_STEP_PIN, OUTPUT);
    // Use an external pulldown and cap for debouncing
    pinMode(END_STOP_PIN, INPUT);

    disable_stepper();

    // Setup variables
    current_steps = 0;
    target_steps = 40;
    calibrated = false;
#ifdef RECOVER_AFTER_RESTART
    if (storage_data_available())
    {
        current_steps = load_current_steps();
        target_steps = load_target_steps();;
        calibrated = true;
    }
#endif // RECOVER_AFTER_RESTART

    return 0;
}

/*
 * This function activates the motor. As it is nonblocking, it has to be 
 * called multiple times until the curtain is fully opened.
 * Uses an internal step target to determine fully opened.
 * 
 * @return: Success status: 1 if not yet opened, 0 if fully opened.
 */
int open_nonblocking()
{
#ifdef PRINTS_AT_EACH_STEP
    printf("Opening...\n");
#endif // PRINTS_AT_EACH_STEP
    if (!calibrated)
    {
#ifdef MOTOR_PRINTS
        printf("Cannot open when the system has not been calibrated!\n\r");
#endif // MOTOR_PRINTS

        return 0;
    }

    if (current_steps >= target_steps)
    {
        // TODO Here the passive break mode could be used instead of disabling.
        disable_stepper();
#ifdef RECOVER_AFTER_RESTART
        store_current_steps(current_steps);
#endif // RECOVER_AFTER_RESTART
        return 0;
    }
    else
    {
        // TODO A check if already enabled could be employed.
        if (!stepper_enabled)
            enable_stepper();
        make_step(0);

        return 1;
    }
}

/*
 * This function activates the motor. As it is nonblocking, it has to be 
 * called multiple times until the curtain is fully closed.
 * Rolls back if the end stop has been reached sooner than expected.
 * 
 * @return: Success status: 1 if not yet closed, 0 if fully closed.
 */
int close_nonblocking()
{
    static bool rollback_necessary = false;
#ifdef PRINTS_AT_EACH_STEP
    printf("Closing...\n");
#endif // PRINTS_AT_EACH_STEP
    if (!calibrated)
    {
#ifdef MOTOR_PRINTS
        printf("Cannot close when the system has not been calibrated!\n\r");
#endif // MOTOR_PRINTS
        return 0;
    }

    // Roll back the motor if the endstop is reached sooner than expected.
    int end_stop = digitalRead(END_STOP_PIN);
    if (end_stop == LOW)
    {
        rollback_necessary = true;
    }

    int motor_status = 1;
    if (rollback_necessary)
    {
        motor_status = rollback();
        if (motor_status == 0)
        {
            rollback_necessary = false;
            disable_stepper();
            current_steps = 0;
        }
    }
    else if ((current_steps <= 0))
    {
        disable_stepper();
        motor_status = 0;
    }
    else
    {
        if (!stepper_enabled)
            enable_stepper();
        make_step(1);
        motor_status = 1;
    }

#ifdef RECOVER_AFTER_RESTART
    if (motor_status == 0)
        store_current_steps(current_steps);
#endif // RECOVER_AFTER_RESTART

    return motor_status;
}

/*
 * This function moves the curtain in the opposite position, I call it xor.
 * This function activates the motor. As it is nonblocking, it has to be 
 * called multiple times until the curtain is fully xored.
 * 
 * @return: Success status: 1 if not yet xored, 0 if fully xored.
 */
int curtain_xor()
{
    static enum CURTAIN_STATE state_when_started = CURTAIN_UNDEFINED_T;

    // Start the curtain XOR
    if (state_when_started == CURTAIN_UNDEFINED_T)
    {
        // When in doubt use OPENED. Use the end stop to abort when closing.
        if (get_curtain_state() == CURTAIN_CLOSED_T)
            state_when_started = CURTAIN_CLOSED_T;
        else // CURTAIN_OPENED_T   *or*   CURTAIN_UNDEFINED_T
            state_when_started = CURTAIN_OPEN_T;
    }

    // Open or close
    int status = 1;
    if (state_when_started == CURTAIN_OPEN_T)
        status = close_nonblocking();
    else
        status = open_nonblocking();

    // Reset the static variable
    if (status == 0)
        state_when_started = CURTAIN_UNDEFINED_T;

    return status;
}
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

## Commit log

2021-09-06 added basic proof of concept code
    [configuration.h]
2021-09-23 Added and tested action executer, basic tests for motor controller
    [configuration.h]
2021-09-23 added state and tests to motor controller
2021-09-23 added alarm checker with a few tests
    [configuration.h]
2021-09-24 removed files to track
2021-09-24 removed files to track 2
2021-09-28 added socket test for esp
2021-09-28 refactored socket test, added get_user_in and user respond_to_user
2021-09-29 rectored typedefs, improved error handling
    [Testsuite.c]
2021-09-30 expanded motor_controller
2021-10-01 added ignore once, fixing warnings
    [configuration.h]
2021-10-07 changes to input parsing, added actual project with user socket
    [configuration.h]
2021-10-10 added dummy data storage, adaptable to eeprom library
    [configuration.h]
2021-10-27 added alarm checker, added calibration rollback
2021-10-29 added basic wiring diagram
    [curtain_wiring.kicad_pcb, curtain_wiring.sch]
2021-10-31 tried and improved calibration with rollback
2021-10-31 fixed local input, improved calibration
    [local_communication.cpp, main.cpp, motor_controller.cpp]
2021-10-31 opening and closing now only works when calibrated, alarm_checker needs to be reworked
    [motor_controller.cpp]
2021-11-02 updated wiring
    [curtain_wiring.sch]
2021-11-03 enabling and disabling steppers at appropriate times
2021-11-10 added local display of button presses
2021-11-11 refactored motor_controller, calibrating without delay
2021-11-11 copied unit tests, stack size too small
    [configuration.h]
2021-11-11 added/removed comments
    [configuration.h]
2021-11-14 3d objects and updated readmes
    [beam_holder_l_longer_v1.stl, beam_holder_r_longer_v1.stl, belt_connector_lid_v1.stl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]
2021-11-14 removed conflicts
    [configuration.h]
2021-12-02 updated 3d models
    [5mm_led_standoff_v1.stl, pcb_holder_v1.stl, tail_tpu_damper_v1.stl]
2022-01-31 added check for head fragmentation
    [configuration.h]
2022-02-06 added recovery after reboot
    [configuration.h, micro_switch_holder_v1.stl]
2022-02-06 added pcb v1
    [curtain_wiring-B_Cu.gbl, curtain_wiring-B_Mask.gbs, curtain_wiring-B_Paste.gbp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]
2022-02-06 added wiring readme
2022-03-15 updated test suite project, mirrored files
    [configuration.h]
2022-03-16 updated comments
    [configuration.h]
2022-03-16 updated wiring readme
2022-03-16 higher res wiring
2022-03-27 small bug fixes
    [configuration.h]
2022-03-27 created a small website prototype, not yet working
2022-04-02 added first website prototype
2022-04-24 added integrated supports to pcb cover
    [pcb_cover_rounded_v2.stl]
2022-08-31 fixed dependencies, restyled the web interface
    [main.cpp, web_communication.cpp]
2022-09-04 updated 3D files, updated readme
    [beam_holder_l_longer_v1.stl, beam_holder_l_longer_v1_1.stl, beam_holder_r_longer_v1.stl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]
2022-09-29 readme, comments
    [configuration.h]
2022-09-30 fixed conflicts
    [configuration.h]
2023-03-30 fix bug of websocketserver not opening
    [configuration.h]
2023-04-02 Moved WiFi connection, added Serial ssid and pw setting
    [configuration.h]
2023-04-05 added working wps, file, eeprom and serial connection
    [configuration.h]
2023-04-24 added class and sequence diagram, ported refactored alarm_checker to esp, increased printability, readme
    [beam_holder_l_longer_v1_1.stl, beam_holder_l_longer_v1_2.stl, beam_holder_r_longer_v1_1.stl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]
